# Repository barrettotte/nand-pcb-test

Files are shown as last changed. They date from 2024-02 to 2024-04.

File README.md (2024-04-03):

# nand-pcb-test

Homemade PCB test using a CNC router.

Hopefully this is useful to someone else wanting a single place to see the whole CNC PCB building process.
These notes assume you have a basic understanding of Kicad and Candle (grblcontrol).

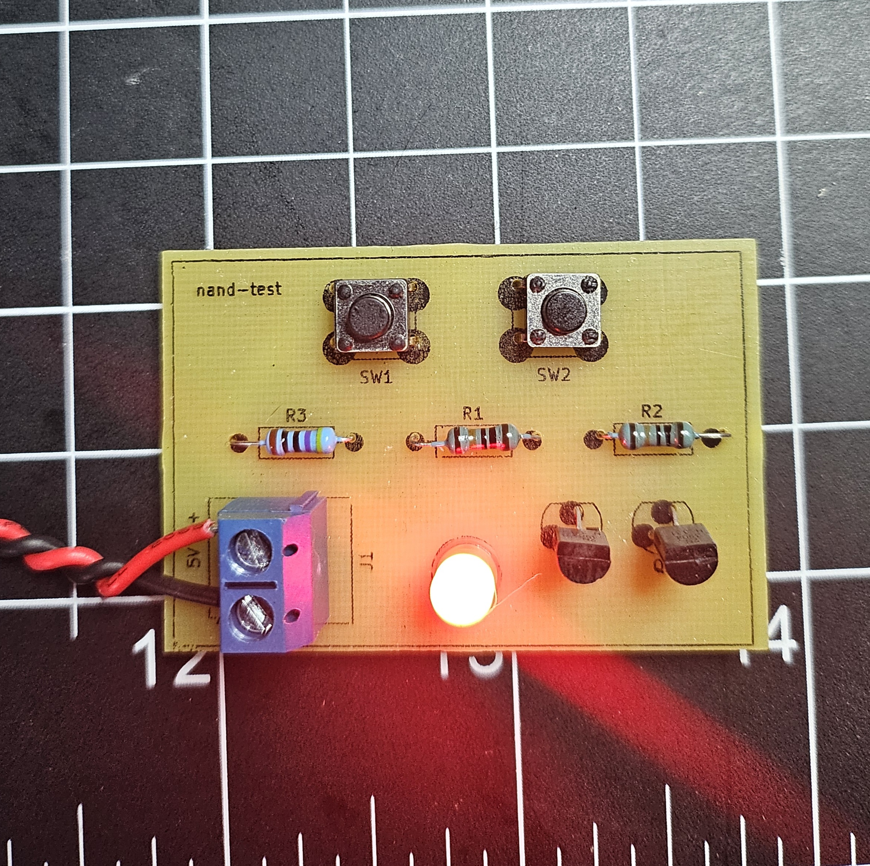
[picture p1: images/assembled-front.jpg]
assembled front


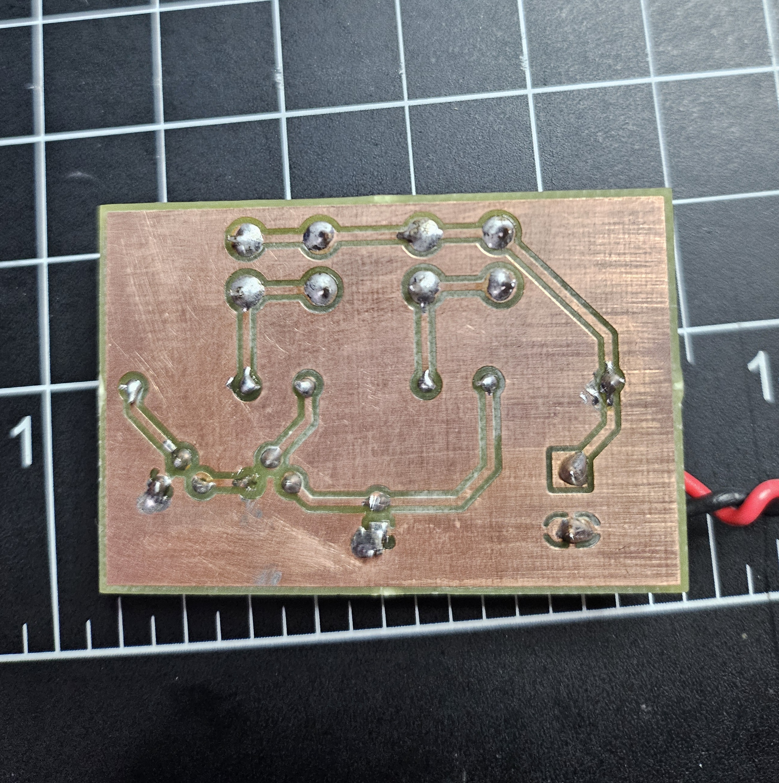
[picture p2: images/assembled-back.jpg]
assembled back


## Why?

There are plenty of companies that offer cheap PCB manufacturing, but I'm impatient and bad at designing things correctly on the first try.
Imagine ordering a PCB, waiting a few days, and figuring out you messed up your design.
Manufacturing with a CNC router helps to eliminate waiting time between idea and implementation.

Alternatively, plenty of people use the chemical etching process (example: thermal transfer paper and ferric chloride) to build their PCBs.
I just don't have a good workspace to mess with nasty chemicals, so the CNC approach is more doable for me.
Maybe I'll also add a chemical etching bonus section in the future.

For 2+ sided PCBs, it would be worth ordering from a company. Double-sided PCBs are possible, but I have not attempted this yet.
I also haven't tried designs with SMD components yet, so that may also be a pain point that warrants ordering PCBs from a company.

## Equipment

- [Genmitsu 3020-PRO MAX V2 CNC Router](https://www.sainsmart.com/collections/new-genmitsu-collection/products/3020-pro-max-v2)
  - [3040 Y-Axis Extension Kit](https://www.sainsmart.com/collections/genmitsu-cnc-replacement-upgrade-parts/products/3020-yaxis-extension-kit) (optional)
- [FR-4 Copper Clad PCB Laminate Board, Single Side, 4 x 2.7 inch (10 piece)](https://www.amazon.com/dp/B01MCVLDDZ)
- Bits
  - [0.5mm PCB End Mill Bit](https://www.amazon.com/gp/product/B073RJ3SYZ)
  - [0.8mm PCB Drill Bit](https://www.amazon.com/gp/product/B091FD44Y3)
  - [2.5mm End Mill Bit](https://www.amazon.com/gp/product/B07P84V888)
  - [Assorted PCB Drill Bit Set](https://www.amazon.com/gp/product/B08M5PLF48)
- [Mini Dry Iron](https://www.amazon.com/gp/product/B09YXVWSTQ)
- [Thermal Transfer Paper](https://www.amazon.com/gp/product/B07GLGL2CX)
- [Monochrome Laser Printer](https://www.amazon.com/gp/product/B00NQ1CLTI)
- [Mini Drill Press](https://www.amazon.com/gp/product/B0BKZRD2P7)

cnc router

## Build Process

### Circuit Design and Prototyping

- Design circuit in Kicad Schematic Editor
- Breadboard implementation
- Protoboard implementation (optional)
- Kicad Schematic Editor
  - Inspect > Electrical Rules Checker
  - Tools > Annotate Schematic
  - Tools > Assign Footprints
  - File > Plot > PDF, Plot All Pages

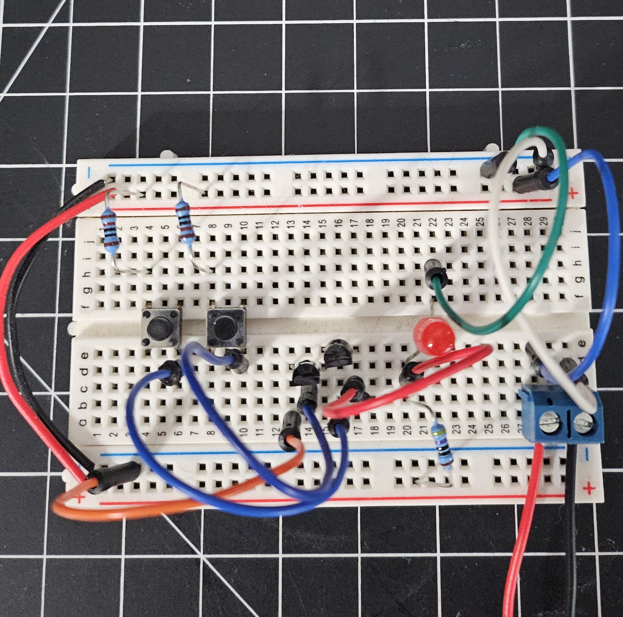
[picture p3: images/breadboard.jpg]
breadboard


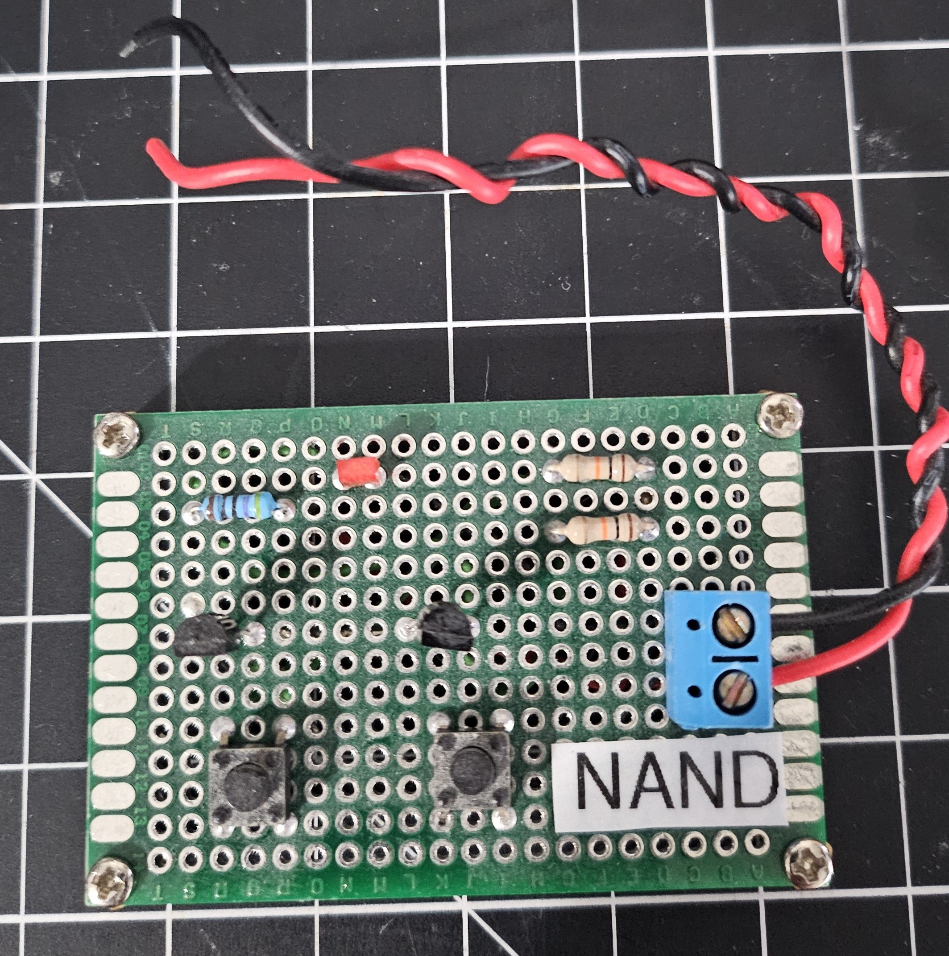
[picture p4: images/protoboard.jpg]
protoboard


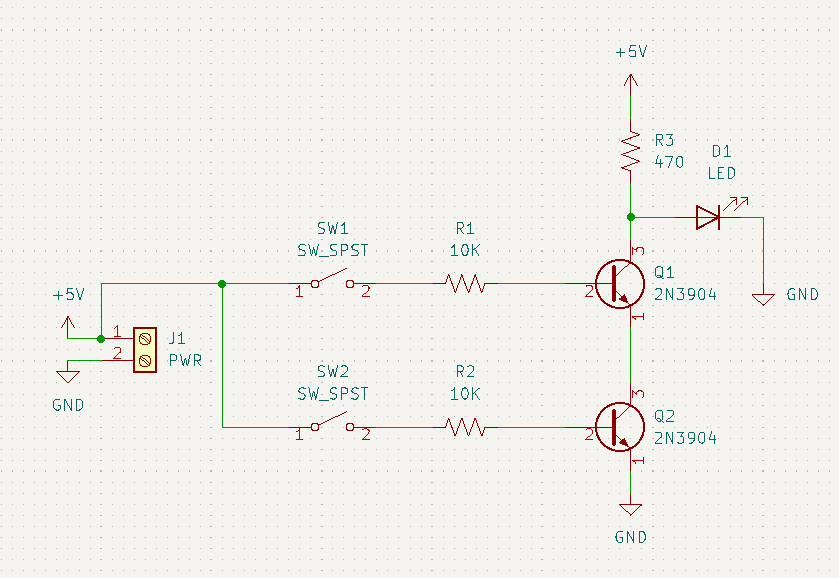
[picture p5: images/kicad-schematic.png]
kicad schematic


### PCB Design

- Open Kicad PCB Editor (or from Kicad Schematic Editor: Tools > Update PCB From Schematic)
- Generally only use back copper and front silkscreen
- Rearrange rats nest of components to eliminate overlap
- Set design rules (File > Board Setup)
  - Minimum clearance: 0.5mm
  - Minimum track width: 0.5mm
  - Copper to hole clearance: 0.5mm
  - Copper to edge clearance: 0.5mm
  - Minimum through hole: 0.7mm
  - Hole to hole clearance: 0.5mm
- Route tracks on `B.Cu` (back copper) layer. Ignore ground pins, will be filled later
- Select `Edge.Cuts` layer, draw a rectangle to trace board boundary, thickness 1mm
- Select `B.Cu` layer and add fill for ground
- Right click fill edge, Zones > Fill Zone
- Add orthogonal dimensions to `User.Drawings` layer to double check board width/height
- Place origin at top left of board
- Run Design Rules Checker
- If exporting `F.Silkscreen`, I recommend setting text thickness to 0.1mm 
- Export Gerber files (File > Plot)
  - Check Use drill/place file origin
  - Export `B.Cu`, `Edge.Cuts` (used in router step)
  - Export `B.Mask` (used in solder masking step) as PDF
  - Generate Drill Files (`*-NPTH.drl` and `*-PTH.drl`)
    - Drill Origin = Drill/place file origin
    - Drill Units = Millimeters
- Print (File > Print) `F.Silkscreen` and `F.Mask` layers to PDF (used in silkscreen step)
  - Verify Print One Page Per Layer is unchecked
  - Scale 1:1
  - Select Print Mirrored

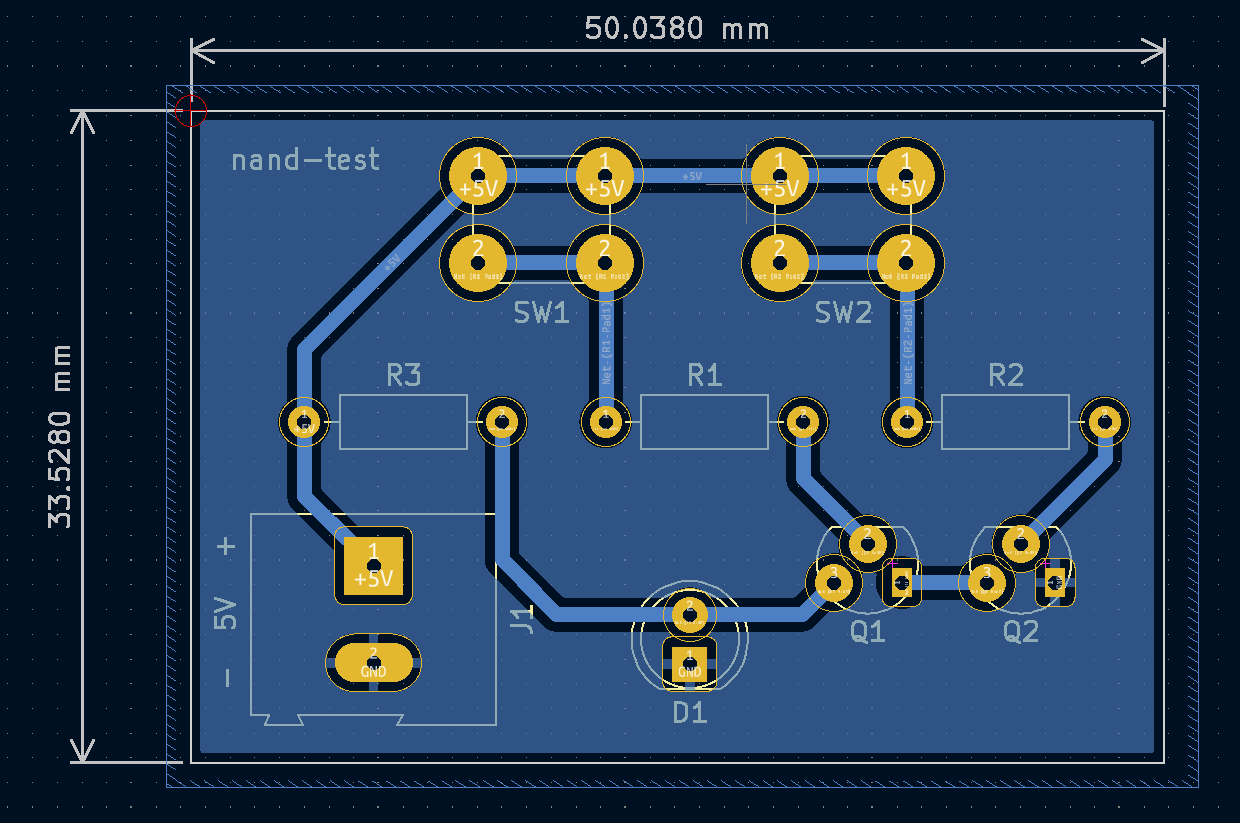
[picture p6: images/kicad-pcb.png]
kicad pcb


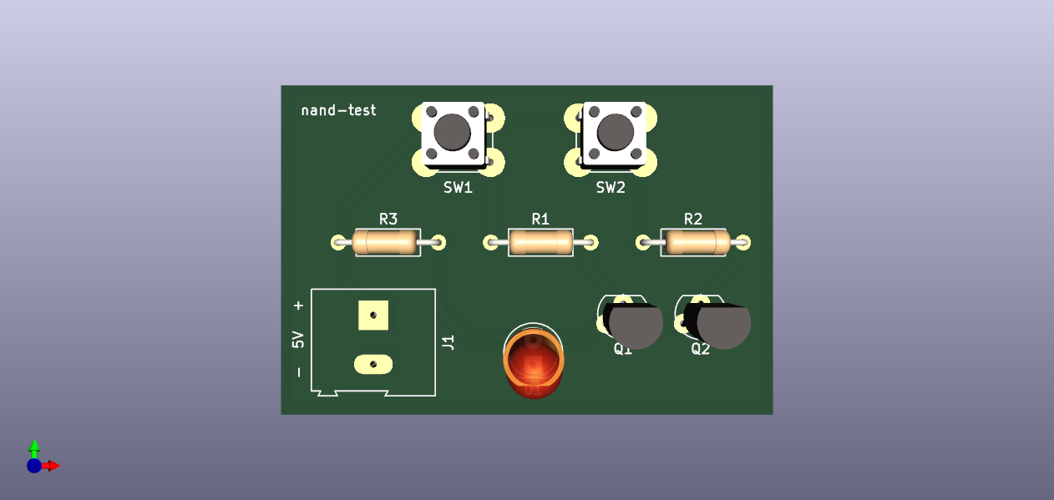
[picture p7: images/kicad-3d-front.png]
kicad pcb 3d front


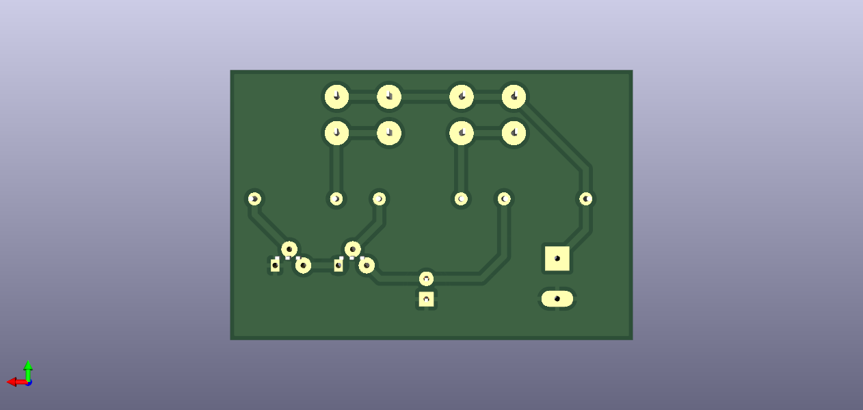
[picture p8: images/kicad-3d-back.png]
kicad pcb 3d back


### Bits

Refer to bits listed in Equipment section above.

- Isolation routing: 0.5mm pcb milling bit
- Holes: 0.8mm drill bit
- Edge cut: 2.5mm end mill bit

I know a lot of people seem to recommend v-bits, but I found them to cut too
inconsistent to quickly throw together boards. 

I did manage to get a couple boards cut with a 0.1mm 60deg bit after manually offsetting my heightmap by 0.05 increments, but I could not replicate this every time. 
Switching to the pcb milling bit removed ~5-10 minutes of manual adjustment.

### Computer Aided Manufacturing (CAM)

- Launch FlatCAM
- Load `B.Cu` and `Edge.Cuts` gerber files (File > Open Gerber)
- Add drill files (`*.drl`) (File > Open Excellon)
  - Note: Ignore "No geometry found in file" error if no NPTH holes needed
- Options tab
  - Set units to mm
- Mirror on y-axis since we're cutting the back copper
  - Tool > Double-Sided PCB Tool
  - Mirror `B.Cu` and `*.drl` files on y-axis using Point/Box
- Select `*-B_Cu.gbr`
  - Isolation Routing section
  - Tool dia: 0.45 (note: 0.05 less than clearance set in Kicad)
  - Width (# passes): 2
  - Pass overlap: 0.10
  - Combine Passes: yes
  - Click Generate Geometry
- Select `*-B_Cu.gbr_iso`
  - Create CNC Job section
  - Cut Z: -0.015
  - Travel Z: 2
  - Feed Rate: 85.0
  - Tool dia: 0.45 (note: 0.05 less than clearance set in Kicad)
  - Spindle speed: 10000
  - Multi-Depth: yes
  - Depth/Pass: 0.08
  - Click Generate
- Select `*-B_Cu.gbr_iso_cnc`, export G-Code to `B_Cu.nc`
- Select `*-PTH.drl`
  - If too many sizes of drills, go back to Kicad and change hole sizes of individual components (we can always redrill by hand later if holes too small)
  - Create CNC Job section
  - Cut Z: -2
  - Travel Z: 2
  - Feed Rate: 100.0
  - Tool Change: no (unless using multiple drill sizes)
  - Spindle Speed: 10000
  - Click Generate
- Select `*-PTH.drl_cnc`, set tool dia to 0.8, export G-Code to `PTH.drl.nc`
- Select `*.Edge_Cuts.gbr`
  - Board cutout section
  - Tool dia: 2.5
  - Margin: 0.1
  - Gap size: 1.0
  - Gaps: 4
  - Click Generate Geometry
- Select `*-Edge_Cuts.gbr_cutout`
  - Create CNC Job section
  - Cut Z: -2
  - Travel Z: 2.0
  - Feed Rate: 50.0
  - Tool dia: 2.5
  - Spindle speed: 10000
  - Multi-Depth: yes
  - Depth/pass: 0.25
  - Click Generate
- Select `*-Edge_Cuts.gbr_cutout_cnc`, export G-Code to `Edge_Cuts.nc`

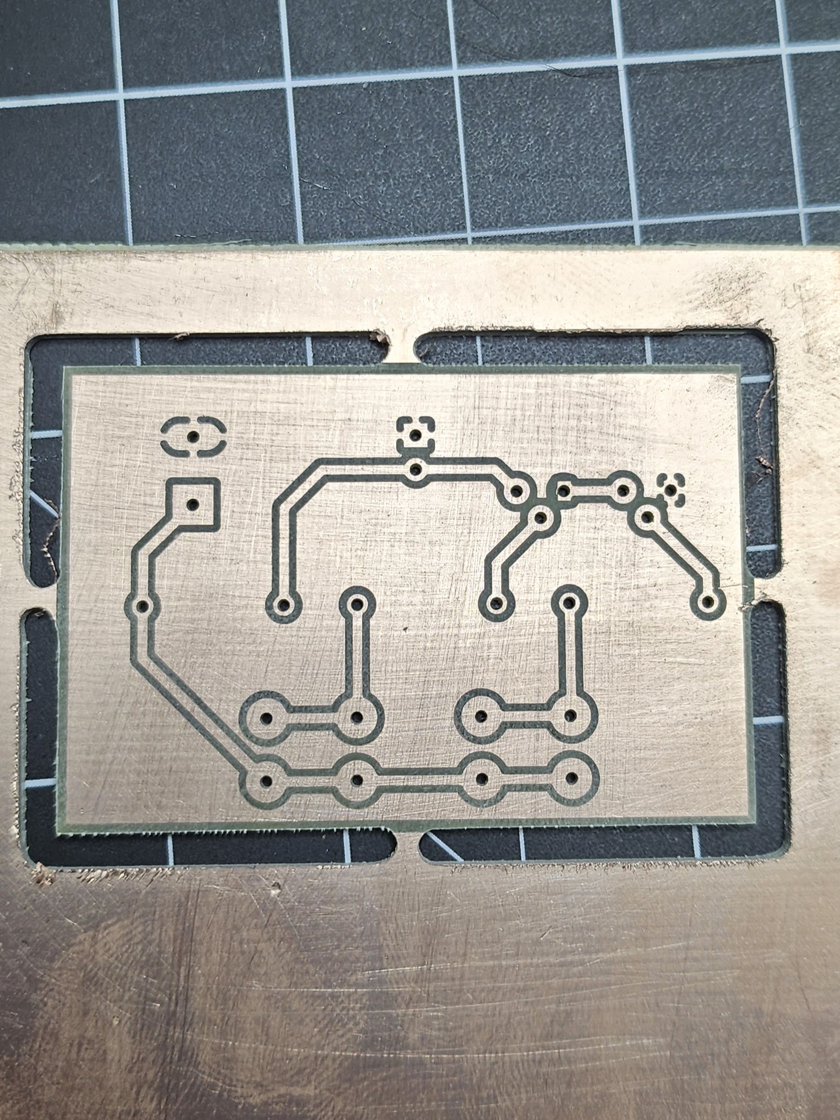
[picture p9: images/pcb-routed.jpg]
routed pcb


### Preparing Silkscreen

- Open `F.Silkscreen` PDF in Inkscape (to remove blank space of PDF document)
  - Select silkscreen components, export
  - Export Selection tab, Export Selected Only, 300.0 DPI, SVG

### CNC Routing

Refer to bits in "Computer Aided Manufacturing (CAM)" section

To secure the PCB to the bed, 
I used 3D printed M6 Plate Clamps from https://www.printables.com/model/250450-enhancements-for-sainsmartgenmitsu-3020-pro-max-cn/files. 
Alternatively, I saw a lot of people using carpet tape.

Probe setup using aluminum tape and z-probe that came with CNC router.

cnc probe setup

- Jog machine to upper left corner, z probe, zero XY
- Height map
  - Load nc file, click auto
  - Zero XYZ, set bit at origin
  - Probe grid, set to be ~10mm apart
  - Interpolation grid: 20, 20
  - zt = 1.0, zb = -1.0
  - Click Probe
  - Save as `height.map`
  - Click edit mode to leave edit mode
  - Verify use heightmap is checked
- Remove probes
- Load `B.Cu.nc`
- Swap to drill bit, re-zero Z
- Load `PTH.drl.nc`
- Swap to edge cut bit, re-zero Z
- Load `Edge_Cuts.nc`

### Silkscreen

- Load thermal transfer paper into printer
- Print `F.Silkscreen` SVG onto thermal transfer paper (smooth side up)
  - Ensure scale is 100%
- Tape thermal paper to front of PCB (toner side down)
- Use highest setting of dry iron to heat evenly for 2-3 minutes
- Apply polycrylic to preserve silkscreen

silkscreen

### Final Steps

- Use mini drill press to adjust any holes for larger through hole parts
- Use 400-600 grit sandpaper and/or steel wool to remove any small burrs on back copper
- File down tabs on sides of PCB
- Clean off with a bit of isopropyl alcohol
- Use multimeter to check all tracks for shorts
- Solder components
- Clean off any flux with isopropyl

assembled front

assembled back

## Archive

I tried to do a couple different steps that I hope to try again in the future.
I left my notes in [archive/](archive/).

## References

- [Candle](https://github.com/trasz/grblControl)
- [FlatCAM](http://flatcam.org/)
- [GCODE Reference](https://marlinfw.org/meta/gcode/)
- Youtube
  - [Homemade custom PCB guide using free KiCAD software; Teaching Tech](https://www.youtube.com/watch?v=NgDXPWaA5Ic)
  - [Homemade PCB using thermal transfer paper](https://www.youtube.com/watch?v=aemG_4sDz_Q)
  - [Intro to Kicad; Shawn Hymel](https://www.youtube.com/playlist?list=PL3bNyZYHcRSUhUXUt51W6nKvxx2ORvUQB)
  - [Machining a PCB on the 3-axis CNC Bridgeport Mill; Usagi Electric](https://www.youtube.com/watch?v=AB84_vbH_e8)
  - [Milling PCBs on a Homemade CNC (Part 2): Masking](https://www.youtube.com/watch?v=qIxvXU7KDmE)
  - [Milling Printed Circuit Boards (PCBs) on a Cheap CNC Machine; Matt's Electronics & RC](https://www.youtube.com/watch?v=bQ6_oYZrsjk)
  - [Relay Calculators: Episode 8 - Using FlatCAM and a CNC mill to make PCBs; Usagi Electric](https://www.youtube.com/watch?v=F2FRN5z2S78)
  - [Sainsmart Genmitsu 3020 Pro Max - 300W Spindle & Linear Rails - Build, Test & Review; techydiy](https://www.youtube.com/watch?v=5vaAthrJQm0)

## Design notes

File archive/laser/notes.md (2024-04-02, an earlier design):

# Laser Notes

I was going to do a laser silkscreen, but I didn't like the workflow
and was struggling to keep things aligned when flipping over a freshly routed board.

## Notes

## Equipment

- [RFL10W 10W Compressed FAC Laser Module](https://www.sainsmart.com/collections/genmitsu-cnc-replacement-upgrade-parts/products/10w-compressed-fac-laser-module-with-air-assist-nozzle-for-genmitsu-cnc-laser-m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)

### Preparing Silkscreen (optional)

- Open in `F.Silkscreen` PDF in Inkscape
  - Select silkscreen components, export
  - Export Selection tab, Export Selected Only, 300.0 DPI, PNG
- Open exported png in LaserGRBL
  - Conversion Tool - Passthrough
  - Click Next
  - Engraving Speed: 1000 mm/min
  - Laser Options, Laser Mode: M3, S-MIN: 0, S-MAX: 800
  - Image Autosize 300 DPI
  - Click Create
  - File > Save Laser GCODE

### Laser Etching Silkscreen (optional)

- Launch LaserGrbl
- Grbl > Settings
  - Jog control tab - Show Z up/down control
- Grbl > Grbl Configuration
  - $30 = 1000 RPM (configures laser power)
  - $32 = 1 (laser mode)
- Turn on laser low power, adjust Z-axis until dot is as small as possible (finding the focal point)

TODO: ...

## References

- [LaserGRBL](https://lasergrbl.com/)
- [3018 Pro - Setting up your laser; James Dean Designs](https://www.youtube.com/watch?v=YnFNFEdmPjU)
- [3018 Pro - Basics for Laser Engraving; James Dean Designs](https://www.youtube.com/watch?v=pCmazk-yTVo)

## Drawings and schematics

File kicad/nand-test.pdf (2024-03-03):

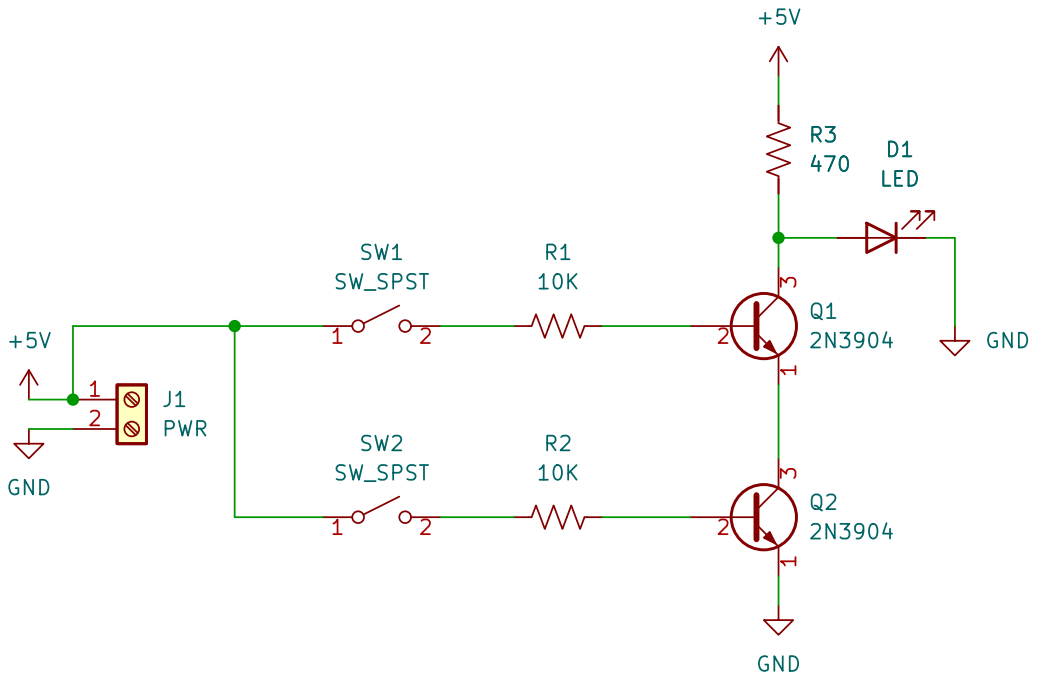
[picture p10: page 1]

https://github.com/barrettotte/nand-pcb-test
File: nand-test.kicad_sch Sheet: / Barrett Otte

Id: 1/1 Title: nand-pcb-test

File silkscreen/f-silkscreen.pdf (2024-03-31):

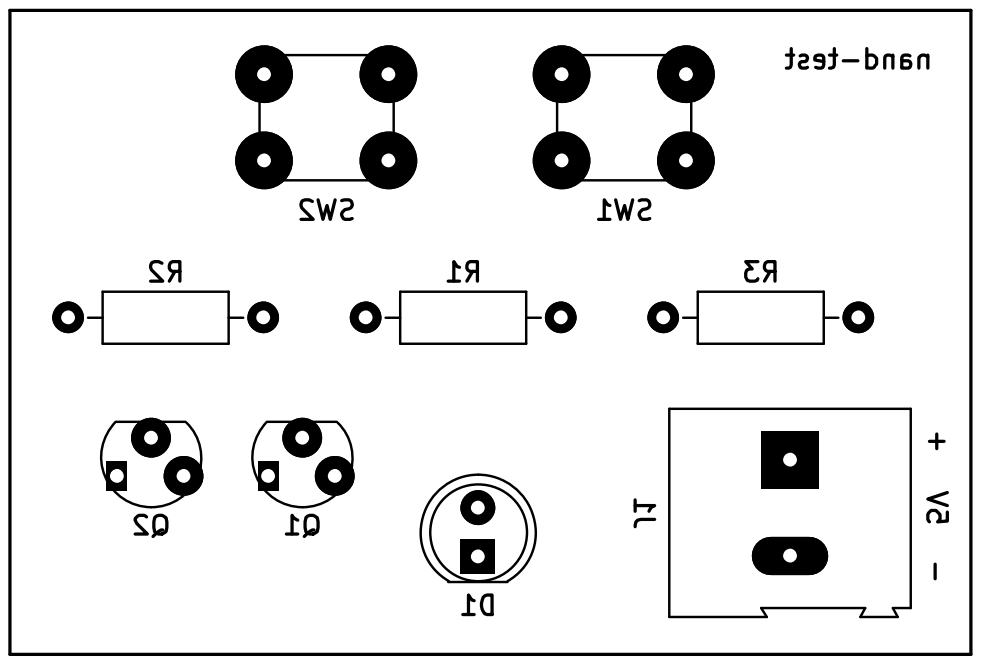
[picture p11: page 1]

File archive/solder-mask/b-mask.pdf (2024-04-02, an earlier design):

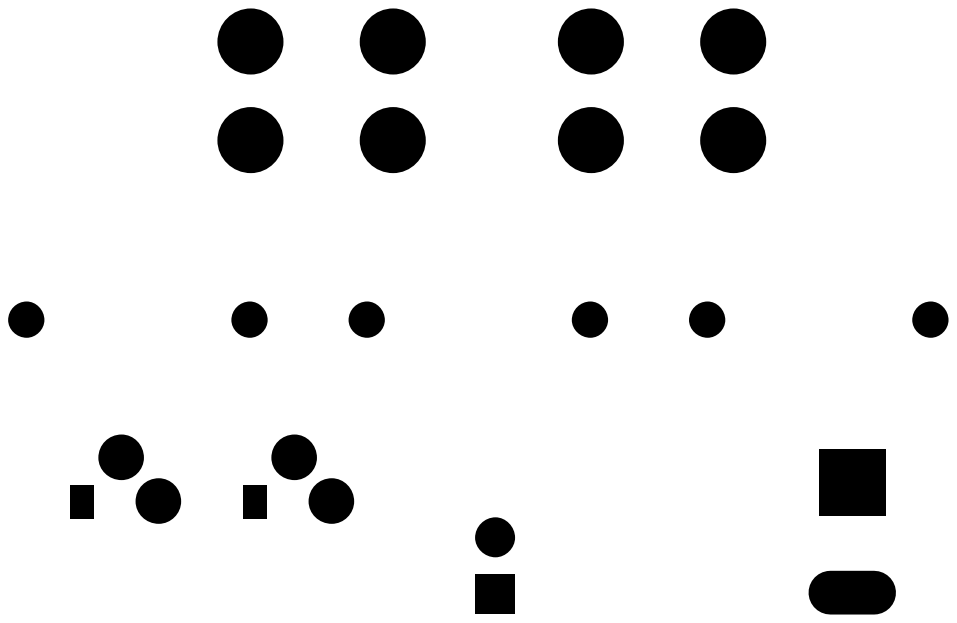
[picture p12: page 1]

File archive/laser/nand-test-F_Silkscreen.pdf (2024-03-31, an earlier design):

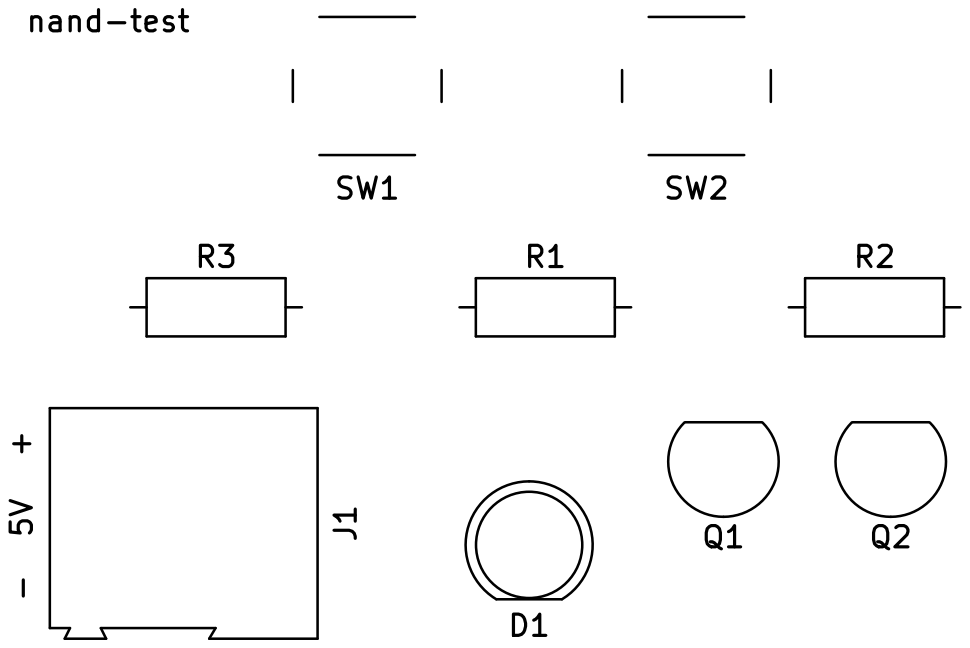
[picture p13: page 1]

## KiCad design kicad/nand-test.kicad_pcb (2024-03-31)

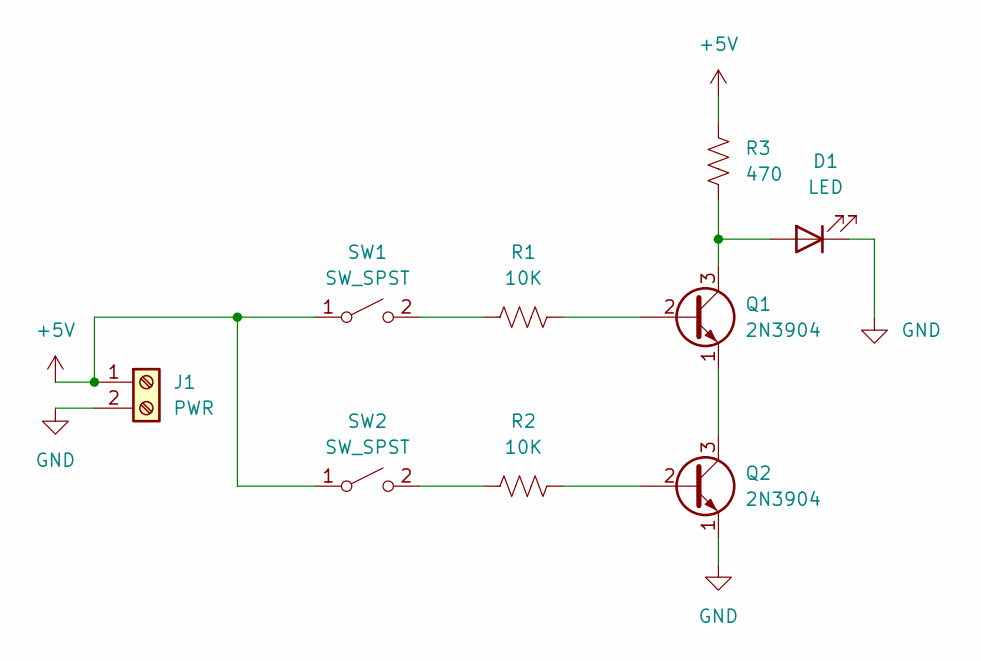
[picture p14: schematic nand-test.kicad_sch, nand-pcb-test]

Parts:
D1: LED; LED_D5.0mm
J1: PWR; TerminalBlock_Altech_AK300-2_P5.00mm
Q1, Q2: 2N3904; TO-92_Inline
R1, R2: 10K; R_Axial_DIN0207_L6.3mm_D2.5mm_P10.16mm_Horizontal
R3: 470; R_Axial_DIN0207_L6.3mm_D2.5mm_P10.16mm_Horizontal
SW1, SW2: SW_SPST; SW_PUSH_6mm

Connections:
+5V: J1.1, R3.1, SW1.1 (A), SW2.1 (A)
GND: D1.1 (K), J1.2, Q2.1 (E)
unnamed: D1.2 (A), Q1.3 (C), R3.2
unnamed: Q1.1 (E), Q2.3 (C)
unnamed: Q1.2 (B), R1.2
unnamed: Q2.2 (B), R2.2
unnamed: R1.1, SW1.2 (B)
unnamed: R2.1, SW2.2 (B)

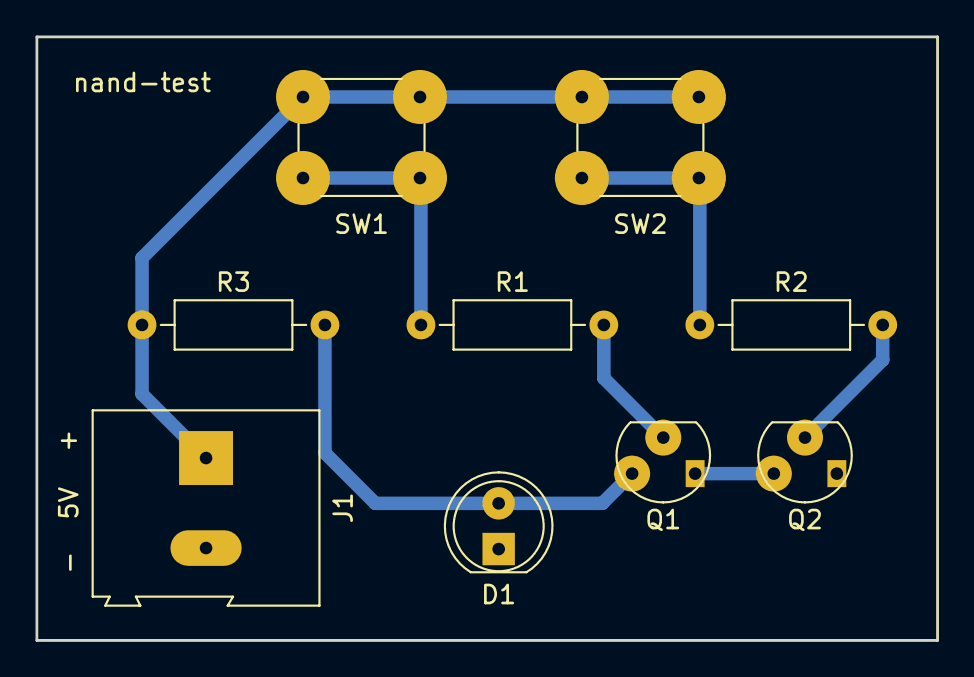
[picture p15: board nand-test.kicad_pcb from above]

Board: 2 copper layers, 50.0 x 33.5 mm, 9 parts (0 on the bottom side), 8 nets.

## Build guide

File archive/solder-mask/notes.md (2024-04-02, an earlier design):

# solder mask notes

I was going to do a solder mask on the back copper, but I couldn't figure out 
how to get a smooth finish.

## Notes

## Equipment

- Transparency film - https://www.amazon.com/gp/product/B078R4DGSB
- UV nail station - https://www.amazon.com/gp/product/B07G31SQZ7
- UV solder mask
  - https://www.amazon.com/gp/product/B07KWV13P9
  - https://www.amazon.com/gp/product/B0C74FDDRM

## Preparing Solder Mask

- Open `B.mask` PDF in Inkscape (to remove blank space of PDF document)
  - Select mask components, export
  - Export Selection tab, Export Selected Only, 300.0 DPI, SVG

## Applying Solder Mask

- Print `B.mask` SVG onto transparent sheet
- Attach board to plexiglass
- Apply thin layer of UV solder mask to PCB
- Put either plastic wrap or a transparent sheet over PCB
- Attach printed transparent sheet to another pane of plexiglass
- Align plexiglass with solder mask "stencil" to PCB
- Firmly press down top plexiglass and try to minimize air bubbes
- Use UV nail station for ~7 minutes

## References

- https://www.youtube.com/watch?v=qIxvXU7KDmE

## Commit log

2024-02-28 base writeup and kicad pcb
    [nand-test.kicad_pcb, nand-test.kicad_sch]
2024-03-03 generated gerber and gcode
    [nand-test.kicad_pcb, nand-test.kicad_sch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]
2024-03-08 updates gerber/gcode files
    [nand-test.kicad_pcb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]
2024-03-09 update gerber and gcode
    [nand-test.kicad_pcb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]
2024-03-18 updates gerbers, gcode, and notes
    [nand-test.kicad_pcb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]
2024-03-31 archives laser silkscreen steps
2024-03-31 adds silkscreen steps
    [nand-test.kicad_pcb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]
2024-04-02 archive solder mask steps
2024-04-03 adds assembled PCB images
